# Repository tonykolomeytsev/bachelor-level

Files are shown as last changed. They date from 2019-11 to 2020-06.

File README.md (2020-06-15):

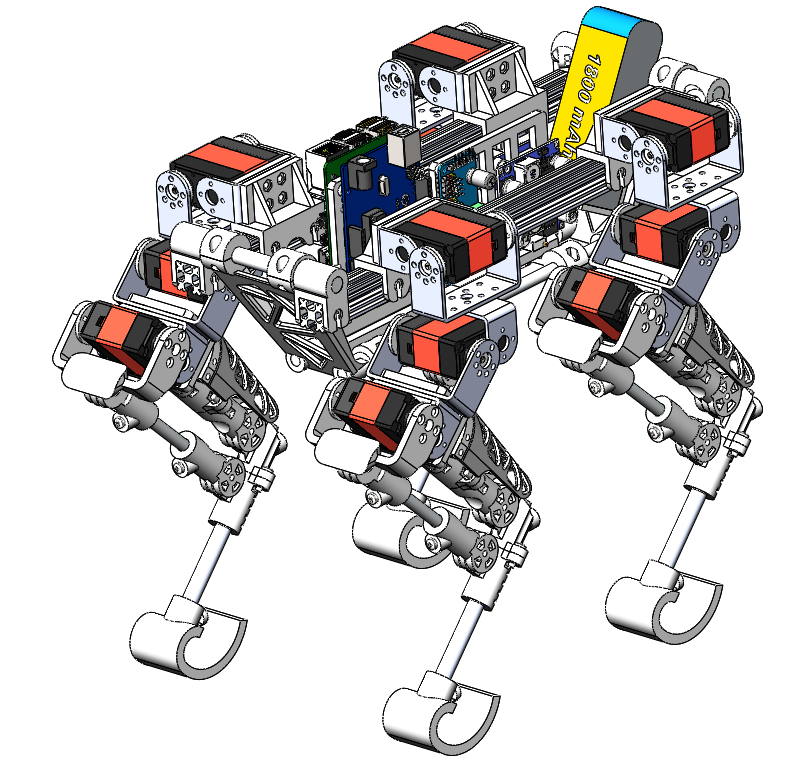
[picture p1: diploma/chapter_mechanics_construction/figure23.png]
Robot drawings


# Бакалаврская работа по разработке прототипа шагающего робота

### О чем вообще работа

В рамках работы рассматривается разработка шагающего четырехногого робота, с упором на проблему разработки конечностей и программирования. Спроектированы трёхмерные твердотельные чертежи системы, собрана физическая модель. Обоснован выбор конструктивных решений, выбор программной архитектуры, выбор алгоритмов. Применены лучшие практики работы с кодом, разработаны программные библиотеки для управления микроконтроллерами в составе робота.

### Материалы

Текст дипломной работы пишется в LATEX. Скомпилированный текст работы можно скачать [здесь](https://github.com/tonykolomeytsev/bachelor-level/raw/master/diploma/index.pdf).

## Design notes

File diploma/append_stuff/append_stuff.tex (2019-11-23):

\append{Комплектующие}
\label{appendix:stuff} % TODO починить нумерацию приложений в ref

\newcommand{\stuffitem}[3]{
    \textbf{#1}\newline
    \begin{tabular}[b]{cc}
         & \begin{tabular}[b]{rl} #3 \end{tabular}
    \end{tabular}
}

\stuffitem{Бесколлекторный двигатель BGM5208-200-12}
{append_stuff/bgm5208_200_12.jpg}
{
    Количество полюсов: & 12 \\
    Внутренний диаметр: & 12мм \\
    Вес: & 85г \\
    Размер: & 63х24мм \\
    Внутр. сопротивление: & 15 Ом
}

\vspace{0.5cm}
\stuffitem{Микрокомпьютер Raspberry Pi 3B}
{append_stuff/rpi.jpg}
{
    Процессор: & Broadcom BCM2837 \\
    Количество ядер: & 4 \\
    Частота процессора: & 1.2ГГц \\
    Разрядность: & 64 бита \\
    Оперативная память: & 1 ГБ \\
    Интерфейсы: & 4xUSB, Ethernet \\
    Напряжение питания: & 5В 
}

\vspace{0.5cm}
\stuffitem{Микроконтроллер STM32 Nucleo F429ZI}
{append_stuff/stm32.jpg}
{
    Ядро: & Cortex M4 \\
    Рабочая частота: & 84 МГц \\
    Разрядность: & 32 бита \\
    Цифровых пинов: & 81 шт. \\
    Кол-во шин: & 3xi2C, 4xSPI \\
    Напряжение питания: & 5В
}

\begin{center}
    \vspace{1cm}
    Продолжение приложения А на следующей странице... \newpage
    Продолжение приложения А...
\end{center}

\vspace{0.5cm}
\stuffitem{Блок питания KMPS05}
{append_stuff/kmps05.png}
{
    Ядро: & Cortex M4 \\
    Рабочая частота: & 84 МГц \\
    Разрядность: & 32 бита \\
    Цифровых пинов: & 81 шт. \\
    Кол-во шин: & 3xi2C, 4xSPI, 3xUART \\
    Напряжение питания: & 5В
}

\vspace{0.5cm}
\stuffitem{Драйвер бесколлекторных двигателей KMBD01}
{append_stuff/kmps05.png}
{
    Ядро: & Cortex M4 \\
    Рабочая частота: & 84 МГц \\
    Разрядность: & 32 бита \\
    Цифровых пинов: & 81 шт. \\
    Кол-во шин: & 3xi2C, 4xSPI, 3xUART \\
    Напряжение питания: & 5В
}

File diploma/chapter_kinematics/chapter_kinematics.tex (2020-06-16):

\chapter{\MakeUppercase{Кинематика конечностей робота}}
\section{Общее положение} \label{sec:kin_general}
Как было сказано ранее, оптимизация распределения массы робота потребовала введения в кинематическую структуру ноги замкнутого контура.
Проблема такой кинематики в механической сложности ее реализации с точки зрения конструктора. Из-за особенностей и требований, описанных в пункте \ref{sec:leg_design}, конструкция ноги получилась, как на рисунке ниже.
\begin{figure}[h]
    \centering
    
    \caption{Чертеж конструкции ноги}
    \label{}
\end{figure}

Для упрощения понимания ниже приведена трехмерная кинематическая схема конечности \ref{fig:kin_scheme}.
\begin{figure}[h] %h!
    \centering
    
    \caption{Трехмерная кинематическая схема ноги робота}
    \label{fig:kin_scheme}
\end{figure}

В составе конечности присутствует непрямой кинематический четырехзвенник (три из четырех сторон имеют разные длины). Это усложнило кинематическую задачу, сделало ее менее тривиальной. Как оказалось далее, наличие четырехзвенной передачи сделало невозможным нахождение аналитического решения обратной задачи кинематики. 

На кинематической схеме отмечены величины, численные значения которых приведены ниже:
\begin{align*} % миллиметры вместо метров и знаки препинания
    a_0&=0 \: мм, \\
    a_1&=46.22 \: мм, \\
    a_2&=20 \: мм, \\
    a_3&=44 \: мм, \\
    a_4&=20 \: мм, \\
    a_5&=27 \: мм, \\
    a_6&=87 \: мм, \\
    a_7&=107 \: мм, \\
    a_8&=12.62 \: мм, \\
    a_9&=24.5 \:  мм, \\
    a_{10}&=110  \: мм
\end{align*}

Заметим, что углы $ \varphi_3 $ и $ \varphi_4 $ различаются из-за того что $ a_5 \neq a_9 $. 

Допустимыми диапазонами рабочих углов являются:
\begin{align*}
    \varphi_1&=0 \dots \frac \pi 8, \\
    \varphi_2&=-\frac \pi 2 \dots 0 ,\\
    \varphi_3&=-\frac \pi 4 \dots \frac \pi 4.
\end{align*}

\noindent здесь границы диапазонов выбраны с запасом, чтобы предотвратить соударения составных частей ноги друг с другом. Диапазон для угла $ \varphi_4 $ не указан, поскольку он зависит от $ \varphi_3 $. 

\section{Общее решение четырёхзвенника} \label{sec:pre_direct_kin}

При построении аналитического решения четырехзвенной передачи было важно подобрать функции так, чтобы для рабочих диапазонов углов $ \varphi_1, \varphi_2, \varphi_3 $ не возникало переходов через ноль, или через бесконечно большие числа. Важно избежать использования кусочных функций и условных операторов для упрощения программирования.
Малые диапазоны углов в рассматриваемой конечности облегчают эту задачу.

На рисунке \ref{fig:scheme_four} приведена схема четырехзвенника. Найдем зависимость $ \varphi_4 $ от $ \varphi_3 $. Здесь $ l= a_4 + a_6=a_7 $ введен для упрощения расчётных формул, т.к. две стороны четырехзвенника имеют одну длину.
\begin{figure}[h]
    \centering
    
    \caption{Четырехзвенник}
    \label{fig:scheme_four}
\end{figure}

Сначала найдем диагональ $d$ по теореме косинусов, для того чтобы выразить противолежащие углы:
\begin{align}
    d = \sqrt{a_5^2 + l^2 - 2a_5 l \cos(\varphi_3)}. \label{eq:kin_1}
\end{align}

\noindent Выразим углы:
\begin{align}
    \gamma &= \text{arcsin}\left(\frac{a_5}{d}\cos \varphi_3\right) \label{eq:gamma}, \\
    \delta &= \text{arccos}\left(\frac{d^2+a_9^2-l^2}{2 a_9 l}\right). \label{eq:delta}
\end{align}

\noindent И искомый угол $ \varphi_4 $ будет находиться следующим образом:
\begin{align}
    \varphi_4 = \pi - \gamma - \delta. \label{eq:phi4_simple}
\end{align}

\noindent Подставим результаты \ref{eq:kin_1}, \ref{eq:gamma}, \ref{eq:delta} в уравнение \ref{eq:phi4_simple} и получим зависимость $ \varphi_4 $ от $ \varphi_3 $:
\begin{multline}
    \varphi_4 = \pi - \text{arcsin}\left(\frac{a_5}{\sqrt{a_5^2 + l^2 - 2a_5 l \cos(\varphi_3)}}\cos \varphi_3\right) - \\ - \text{arccos}\left(\frac{a_5^2 + l^2 - 2a_5 l \cos(\varphi_3)+a_9^2-l^2}{2 a_9 l}\right) .
\end{multline}

\section{Прямая кинематика}\label{sec:direct_kinematics}
Используя найденную в пункте \ref{sec:pre_direct_kin} связь, найдем решение задачи о положении точки $ A $. Трехмерная кинематическая схема приведена на рисунке \ref{fig:kin_scheme}. Зафиксируем сначала первую степень свободы ($ \varphi_1 = 0 $) и найдем координаты точки $ A $ в плоскости, параллельной плоскости $ XZ $:
\begin{multline}
    X_A=a_2+a_3\cos(\varphi_2)+a_6\sin(\varphi_2)-\\-a_8 \cos(\varphi _2+\varphi _4)+(a_9+a_{10}) \sin(\varphi _2+\varphi _4) ,
\end{multline}
\begin{multline} % написать вертикальную черту и phi1=0
    Z_A\Bigr|_{\varphi_1=0} =a_1-a_3 \sin(\varphi _2)+a_6 \cos(\varphi _2)+\\+a_8 \sin(\varphi _2+\varphi _4)+(a_9+a_{10}) \cos(\varphi _2+\varphi _4).
\end{multline}

\noindent Если мы предположим, что $ \varphi_1 = \frac \pi 2 $, тогда конечность будет <<поднята над землей>> в таком положении. Координата $ Z $ точки $ A $ станет равна нулю, координата $ Y $ увеличится. Так как от $ \varphi_1 $ зависят только координаты $Y$ и $Z$, получим следующие уравнения для координат точки $A$:
\begin{multline}
    X_A=a_2+a_3\cos(\varphi_2)+a_6\sin(\varphi_2)-\\-a_8 \cos(\varphi _2+\varphi _4)+(a_9+a_{10}) \sin(\varphi _2+\varphi _4) ,
\end{multline}
\begin{multline}
    Y_A=a_0+\sin(\varphi_1)[a_1-a_3 \sin(\varphi _2)+a_6 \cos(\varphi _2)+\\+a_8 \sin(\varphi _2+\varphi _4)+(a_9+a_{10}) \cos(\varphi _2+\varphi _4)] ,
\end{multline}
\begin{multline}
    Z_A=\cos(\varphi_1)[a_1-a_3 \sin(\varphi _2)+a_6 \cos(\varphi _2)+\\+a_8 \sin(\varphi _2+\varphi _4)+(a_9+a_{10}) \cos(\varphi _2+\varphi _4)].
\end{multline}

\noindent Таким образом, прямая задача кинематики решена.

Получив решение прямой задачи кинематики построим <<рабочую область>> ноги в системе координат связанной с корпусом. Если зафиксировать первую степень свободы, $ \varphi_1 = 0 $, то рабочая область ноги будет лежать в плоскости $ XZ $ (рисунок~\ref{fig:rab_obl}).
\begin{figure}[h]
    \centering
    
    \caption{Сечение рабочей области конечности робота}
    \label{fig:rab_obl}
\end{figure}

Следует отметить, что из-за того что $ a_9 < a_5 $, диапазон углов $ \varphi_4 $ получился шире, чем у $ \varphi_3 $. Это наглядно можно продемонстрировать на проекции ноги на плоскость $ XZ $. На рисунке~\ref{fig:leg_model} синей точкой отмечено реальное положение точки $ A $. Красной точкой отмечено положение точки $ A $ в том случае, если бы в четырехзвеннике $ a_5 $ был равен $ a_9 $. В крайних положениях третье звено конечности поворачивается на угол немного больший, чем угол поворота вала сервопривода. C использованием формулы прямой кинематики на рисунке~\ref{fig:leg_model} были изображены предельные положения последнего звена.
\begin{figure}[ht]
    \centering
    % левая картинка
    \begin{subfigure}[b]{0.45\textwidth}    
        \centering
        
        \caption{}
    \end{subfigure}
    % правая картинка  
    \begin{subfigure}[b]{0.45\textwidth}
        \centering
        
        \caption{}
    \end{subfigure}

    \captionsetup{justification=centering}
    \caption{Проекция ноги на плоскость $ XZ $: \\ (a) третье звено полностью <<разогнуто>>; \\ (б) третье звено полностью <<согнуто>>.}
    \label{fig:leg_model}
\end{figure}

Так, за счет использования четырехзвенной передачи, увеличена рабочая область конечности. На рисунке \ref{fig:fig7} серая область -- рабочая область при $ a_5 = a_9 $, зеленая область -- расширение рабочей области при $ a_5 > a_9 $.
\begin{figure}[h]
    \centering
    
    \caption{Сравнение рабочих областей}
    \label{fig:fig7}
\end{figure}

\section{Обратная кинематика} \label{sec:inverse_kin}
Как уже упоминалось ранее в пункте \ref{sec:kin_general}, аналитическое решение для задачи обратной представляет большую сложность. Это значит что нужно использовать численные методы решения.

Найдем решение обратной задачи кинематики с помощью метода Ньютона.

Кратко опишем суть метода Ньютона для решения системы нелинейных уравнений. 

Пусть дана система из $ n $ нелинейных уравнений с $ n $ неизвестными:
\[
\left\{ 
\begin{array}{c}
    f_1(x_1, \dots, x_n) = 0, \\
    f_2(x_1, \dots, x_n) = 0, \\
    \vdots \\
    f_i(x_1, \dots, x_n) = 0, \\
\end{array} 
\right.
\]

\noindent где $ f_i(x_1,\dots,x_n): \mathbb{R}^n \rightarrow \mathbb{R}, i=1,\dots, n $ -- нелинейные функции, определенные и непрерывно дифференцируемые в некоторой области $ G \subset \mathbb{R}^n $. Для записи в векторном виде введем величины:
\begin{align*}
    \overline{x} &= [x_1, x_2, \dots x_n]^T, \\
    F(x) &= [f_1(x), f_2(x),\dots,f_n(x)]^T = 0
\end{align*}

Нужно найти такой вектор $ \overline{x}^*=[x_1^*, x_2^*, \dots x_n^*]^T $, чтобы было верно равенство $ F(\overline{x}^*) = 0 $. 

Решение уточняется с помощью итерационной процедуры:
\begin{align*} % 
    x^{(k+1)}=x^{(k)}-J^{-1}(x^{(k)}) \cdot F(x^{(k)}),
\end{align*} % уточнить что такое k

\noindent где $ k=1,2\dots $ -- номер итерации, $ x^{(k)} $ -- $k$-е приближение к корню $ \overline{x}^* $, а $ J $ -- матрица Якоби:
\begin{align*}
    J = \begin{bmatrix}
        \frac{\partial f_1}{\partial x_1} & \dots & \frac{\partial f_1}{\partial x_n} \\
        \vdots & \ddots & \vdots \\
        \frac{\partial f_n}{\partial x_1} & \dots & \frac{\partial f_n}{\partial x_n}
    \end{bmatrix}.
\end{align*}

Применительно к задаче, рассматриваемой в данной работе, вектор $ \overline{x} $ является  вектором углов $ \overline{\varphi} = [ \varphi_1, \varphi_2, \varphi_3 ]^T $. Вектор $ F(x) $ -- это правая часть уравнений прямой кинематики.
\begin{equation*}
    F(\overline{\varphi}) = [ X_A(\overline{\varphi}) - X_A^*, Y_A(\overline{\varphi}) - Y_A^*, Z_A(\overline{\varphi}) - Z_A^* ]^T,
\end{equation*}
где $ X_A^*, Y_A^*, Z_A^* $ -- координаты целевого положения точки $A$.

В качестве критерия остановки итераций используется выполнение условия $ \norm{F(\varphi^{(k)}) - F^* } < \varepsilon $, где $\varepsilon $ -- заданная точность позиционирования.

Алгоритм поиска решения обратной задачи представлен ниже. В нём $ \varphi^{(0)} $ -- начальное приближение, $ \varepsilon $ -- точность вычислений, $ i $ -- число итераций (перед выполнением алгоритма устанавливается равным нулю).
\begin{itemize}
    \item[1.] Расчёт Якобиана $$ J = \begin{bmatrix}
        \frac{\partial X_A}{\partial \varphi_1} & 
        \frac{\partial X_A}{\partial \varphi_2} & 
        \frac{\partial X_A}{\partial \varphi_3} \\ \\
        \frac{\partial Y_A}{\partial \varphi_1} & 
        \frac{\partial Y_A}{\partial \varphi_2} & 
        \frac{\partial Y_A}{\partial \varphi_3} \\ \\
        \frac{\partial Z_A}{\partial \varphi_1} & 
        \frac{\partial Z_A}{\partial \varphi_2} & 
        \frac{\partial Z_A}{\partial \varphi_3}
    \end{bmatrix} $$ с использованием формул численного дифференцирования (аналитическая зависимость очень громоздкая).
    \item[2.] Вычисление погрешности: $$ r=F(\varphi^{(k)}). $$
    \item[3.] Вычисление вектора полного шага: $$ p = J^{-1} \cdot r $$ где $ J^{-1} $ -- обратная матрица Якобиана.
    \item[4.] Расчет следующего приближения: $$ \varphi^{(i+1)}=\varphi^{(i)} - p. $$ 
    \item[5.] Если заданная точность не достигнута и не превышен лимит на количество итераций, возвращаемся к пункту 1.
\end{itemize}

\noindent На практике оказалось, что скорость сходимости и сама сходимость сильно зависят от начального приближения. После реализации алгоритма были выявлены две проблемы в его работе:
\begin{itemize}
    \item[1.] Невозможно подобрать такие начальные приближения, при которых бы метод сходился во всем трехмерном пространстве рабочей области.
    \item[2.] В областях, в которых метод сходился в большом удалении от начального приближения, требовалось более 15 итераций для нахождения решения с заданной точностью.
\end{itemize}

\noindent Вторая проблема связана с производительностью вычислений, которые нужно производить на микрокомпьютере в режиме реального времени. Быстрое решение обратной задачи для любой точки трехмерной рабочей области -- это основное требование которое ставилось в начале разработки системы, поэтому итеративное приближение из предыдущих точек не  подходит в данной ситуации. В следующем пункте приведено решение возникших проблем.

\section{Оптимизация численного решения обратной задачи}

Путем проб и ошибок было решено сохранять в памяти (кэшировать) результаты вычислений прямой кинематики во время запуска программы. Проще говоря, подготовить набор заранее рассчитанных начальных приближений, которые будут использоваться от момента запуска робота до момента завершения работы. Во время решения обратной задачи нужно искать в кэш-таблице ближайшее готовое решение, принимать его за начальное условие текущей задачи и от него досчитывать более точное решение.

В качестве первой реализации две сотни предрассчитанных решений были помещены в кэш-таблицу. Каждая запись в таблице имеет две колонки. В первой колонке помещается вектор координат $ [X_A,Y_A,Z_A] $, во второй колонке вектор соответствующих им углов звеньев $ [\varphi_1, \varphi_2, \varphi_3] $. В момент поиска наилучшего начального приближения для некоторого положения конечности $ [X_A^*,Y_A^*,Z_A^*] $ находится такая запись кэш-таблицы, для которой евклидово расстояние между $ [X_A^*,Y_A^*,Z_A^*] $ и $ [X_A,Y_A,Z_A] $ будет минимально. 

\noindent Простейшая реализация кэширования решений обратной кинематики:

\begin{python}
def cache_inversed_kinematics():
    global cache
    cache = []
    phi1_start, phi1_end = PHI1_RANGE
    phi2_start, phi2_end = PHI2_RANGE
    phi3_start, phi3_end = PHI3_RANGE
    
    for phi1 in np.linspace(phi1_start, phi1_end, num=2):
        for phi2 in np.linspace(phi2_start, phi2_end, num=10):
            for phi3 in np.linspace(phi3_start, phi3_end, num=10):
                angles = [phi1, phi2, phi3]
                cache.append((direct(angles), np.array(angles)))
\end{python}

\noindent Пример реализации поиска решения в кэше:

\begin{python}
def find_nearest_solution(coordinates):
    global cache
    return min(cache, key=lambda di: np.linalg.norm(
        (coordinates - di[0]), 
        ord=2
    ))[1]
\end{python}

Так, получилось решить сразу две проблемы, описанные в пункте \ref{sec:inverse_kin}. Теперь на всей рабочей области обеспечена сходимость алгоритма. Поиск по кэш-таблице гораздо менее затратен, чем итерации метода Ньютона, а после того как найдено <<ближайшее>> решение, метод Ньютона быстро досчитывает ответ в среднем за 2-3 итерации.

\noindent Реализация функции поиска решения обратной задачи выглядит так:
\begin{python}
def inversed(coordinates):
    """ 
    Param coordinates is [X, Y, Z] numpy vector, in meters.
    This function uses Newton's numerical method.
    """
    phis = find_nearest_solution(coordinates)
    error = np.ones((3,), dtype=np.float64)
    i = 0
    while np.linalg.norm(error, 2) > 1e-5 and i < 100:
        J = jacobian(phis)
        X = direct(phis)
        error = X - coordinates
        p = np.matmul(np.linalg.pinv(J), error)
        phis = phis - p
        i += 1
    
    return phis
\end{python}

\textbf{Пути для дополнительной оптимизации:}
\begin{itemize}
    \item[1.] Проследить за равномерным распределением кэшированных решений в пространстве рабочей области. В случае равномерного распределения, размер кэша можно сильно уменьшить. Это ускорит поиск по таблице.
    \item[2.] Уменьшать количество кэшированных решений до тех пор пока метод Ньютона продолжает быстро сходиться. Это так же позволит сократить размер кэша и увеличить скорость поиска по нему.
    \item[3.] Найти максимальное значение точности $ \varepsilon $ с учетом ошибок сервоприводов и люфтов конструкции робота. 
\end{itemize}

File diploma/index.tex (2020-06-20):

\documentclass[a4paper,14pt,russian]{extreport}

\usepackage{extsizes}       % для установки размера шрифта
\usepackage{mathtext}       % русские буквы в формулах
\usepackage{cmap}           % поиск в pdf
\usepackage[T2A]{fontenc}   % кодировка
\usepackage[utf8]{inputenc} % кодировка исходного текста
\usepackage[russian]{babel} % локализация и переносы
\usepackage{pscyr}

% далее две строки отвечающие за т.н. "полуторный интервал"
% плюс исправляем кабанические отступы вокруг формул
\usepackage[nodisplayskipstretch]{setspace}
\onehalfspacing
% двойной оттступ - эквивалент интервала который в ворде называют "1.5 отступ"
% но я буду юзать ИСТИННЫЙ полуторный интервал, который на 10% меньше
%\doublespacing 
\parskip 1.5ex % paragraph spacing
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
\usepackage{listings}
\definecolor{mygray}{rgb}{0.5,0.5,0.5} % цвет комментариев
\definecolor{mygreen}{rgb}{0.1,0.6,0.1} % цвет номеров строк
\definecolor{mypurple}{rgb}{0.7,0.1,0.4} % цвет номеров строк
% настройка общего внешнего вида для всех языков
\lstset{breaklines=true,
        basicstyle=\footnotesize\ttfamily,
        commentstyle=\color{mygreen},
        keywordstyle=\bfseries\color{blue},
        stringstyle=\bfseries\color{mypurple},
        numbers=none} %left}
        %numberstyle=\color{mygray},
        %numbersep=20pt}
% Окружения для разных языков программирования
\lstnewenvironment{python}[1][]{\lstset{language=Python,#1}}{}
\lstnewenvironment{cpp}[1][]{\lstset{language=C,#1}}{}
\lstnewenvironment{code}[1][]{\lstset{#1}}{} % для любого кода

% ====================================================================
%                 Организация рабочего пространства
% ====================================================================
\usepackage{import}
\newcommand{\includechapter}[1]{\subimport{chapter_#1/}{chapter_#1}\newpage}
\newcommand{\includeappend}[1]{\subimport{append_#1/}{append_#1}\newpage}
\usepackage{tabularx}

% ====================================================================
%                         Список литературы
% ====================================================================
\newcommand{\includebiblio}[1]{
    \begingroup
    \renewcommand{\chapter}[2]{
        \clearpage
        \stepcounter{chapter}
        \centering\paragraph{\MakeUppercase{Библиографический список}}
        \addcontentsline{toc}{likechapter}{\MakeUppercase{Библиографический список}}
    }
    \let\bibfont\protect\normalsize
    \bibliographystyle{ugost2008} % Стиль библиографических ссылок БибТеХа
    \bibliography{#1}
    \endgroup
}

% ====================================================================
%                           Приложения
% ====================================================================
\usepackage[title,titletoc]{appendix}
\titleformat{\paragraph}[display]
    {\filcenter}
    {\MakeUppercase{\chaptertitlename} \thechapter}
    {8pt}
    {\bfseries}{}
\titlespacing*{\paragraph}{0pt}{-30pt}{8pt}
\newcommand{\append}[1]{
    \clearpage
    \stepcounter{chapter}
    \begin{center}
        \paragraph{\MakeUppercase{\chaptertitlename~\Asbuk{chapter}}}
        \vspace{-0.5cm}
        \paragraph{\MakeUppercase{ #1}}
    \end{center}
    \addcontentsline{toc}{likechapter}{\MakeUppercase{\chaptertitlename~\Asbuk{chapter}: #1}}
}

% ====================================================================
%             Счетчики страниц, таблиц, изображений
% ====================================================================
\usepackage{lastpage} % использовать можно \pageref*{LastPage}
% далее костыль со stackoverflow
\usepackage{totcount}
\newcounter{totfigures}
\newcounter{tottables}
\makeatletter
    \AtEndDocument{
      \addtocounter{totfigures}{\value{figure}}
      \addtocounter{tottables}{\value{table}}
      \immediate\write\@mainaux{
        \string\gdef\string\totfig{\number\value{totfigures}}
        \string\gdef\string\tottab{\number\value{tottables}}   
      }
    }
\makeatother
% перед каждым вызовом chapter обновляем счетчики
\usepackage{etoolbox}
\pretocmd{\chapter}{\addtocounter{totfigures}{\value{figure}}}{}{}
\pretocmd{\chapter}{\addtocounter{tottables}{\value{table}}}{}{}

% ====================================================================
%                           МЕТА-ДАННЫЕ
% ====================================================================
\usepackage{authblk}
\author{Коломейцев А.А.}
\title{Разработка прототипа четырехногого шагающего робота}
\affil{НИУ "МЭИ"}

\newcommand{\fixme}{\color{red} \textbf{FIXME} \color{black}}
\usepackage{pdfpages}

% ====================================================================
%                           НАЧАЛО КОНТЕНТА
% ====================================================================
\begin{document}

\setcounter{page}{4}

\includechapter{annotation} % аннотация

% Оглавление. 
% Для правильного отображения оглавления документ должен быть
% скомпилирован дважды (иногда трижды).
\tableofcontents\newpage

\includechapter{intro} % введение

\includechapter{legged_robots}

\includechapter{mechanics_construction}

\includechapter{kinematics}

% \includechapter{body_orientation} % на удаление

\includechapter{walking_model} % вернуть после ревью

\includechapter{arch}

\includechapter{conclusion}

%\includechapter{system_analisys} % глава "Анализ системы"

\includebiblio{sources} % в файле source.bib лежит БД со списком источников

%Дипломная работа \pageref{LastPage}~с \totfig~рис. \tottab~таблиц.

\appendix

\newpage
\addcontentsline{toc}{likechapter}{ПРИЛОЖЕНИЕ А: ПОСТРОЕНИЕ РАБОЧЕЙ ОБЛАСТИ}
\includepdf[pages={1,2}]{append1.pdf}

% \includeappend{stuff}

% \append{Код класса}
% \lstinputlisting[language=Python,firstline=14,lastline=34,firstnumber=14]{asynclapi.py}

\end{document}

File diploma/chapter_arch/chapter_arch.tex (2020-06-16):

\chapter{\MakeUppercase{Программная архитектура}} \label{chap:arch}
\section{Структура управления}

Высокоуровневая логика запрограммирована на микрокомпьютере \textit{Rasp}-\textit{berry Pi}. Тот в свою очередь отправляет последовательность команд на платформу \textit{Arduino}, которая управляет сервоприводами через специальный драйвер и отправляет информацию о своем состоянии в виде обратной связи на микрокомпьютер. Упрощенная схема реализованной системы приведена на рисунке \ref{fig:upravlenie}.

\begin{figure}[h!]
    \centering
    
    \caption{Упрощенная схема системы управления робота}
    \label{fig:upravlenie}
\end{figure}

\section{Протокол передачи данных} \label{sec:protocol}
Отправка команд от \textit{Raspberry Pi} к \textit{Arduino} и последующий прием обратной связи производится через интерфейс \textit{Serial}. Это самый надежный вариант при условии, что для установки соединения используется обыкновенный \textit{USB} кабель, который уже защищен от помех и штекер которого надежно закреплен в разъеме.

Для достижения наилучшей скорости реакции микроконтроллера на команды был разработан специальный протокол передачи данных и были написаны легковесные программные библиотеки. Для платформы \textit{Arduino} код написан на языке \textit{C++}, для микрокомпьютера \textit{Raspberry Pi} была разработана библиотека на языке \textit{Python}.

\noindent Библиотека для передачи данных написана для трёх платформ. Она сильно упрощает наладку управления \textit{Arduino} с помощью \textit{Raspberry Pi}. Основная идея программного кода в том, чтобы микрокомпьютер отправлял на микроконтроллер очень простые команды, состоящие из массива байт, в который зашифрованы лишь целочисленный номер и вещественные аргументы. Обратная связь от микроконтроллера реализована в формате \textit{JSON}.

\begin{figure}[h]
    \centering
    
    \caption{Управление микроконтроллерами с помощью \textit{Raspberry Pi}}
    \label{}
\end{figure}

\textbf{Для справки}: \textit{JSON} это сокращение от \textit{JavaScript Object Notation} -- формата передачи данных. Как можно понять из названия, \textit{JSON} произошел из \textit{JavaScript}, но он доступен для использования на многих других языках, включая \textit{Python, Ruby, PHP} и \textit{Java}, в англоязычным странах его в основном произносят как \textit{Jason}, то есть как имя Джэйсон. Легкочитаемый и компактный, \textit{JSON} представляет собой хорошую альтернативу \textit{XML} и требует куда меньше форматирования контента \cite{Jayson2018}.

\noindent Объект \textit{JSON} это набор данных в формате <<ключ-значение>>, который находится в фигурных скобках.
Вот так выглядит \textit{JSON} объект:
\begin{code}
{
  "first_name" : "Anton",
  "last_name" : "Kolomeytsev",
  "location" : "Moscow",
  "online" : true,
  "languages" : ["Russian", "English"] 
}
\end{code}

Массив байт, отправляемый на микроконтроллер, всегда имеет одну и ту же структуру, которую легко расшифровать. Каждая команда имеет свой идентификатор (число от 0 до 255), а также может не иметь вовсе, либо иметь ограниченное числом $ 256^4 $ количество аргументов. 

При отправке инструкции на микроконтроллер первым байтом всегда идет номер (идентификатор) команды. Вторым байтом идет число -- количество аргументов. Если у команды нет аргументов, байт нулевой. Пример команды без аргументов с идентификатором $ 207 $:
\begin{equation*}
    \overbrace{11001111}^{идентификатор\: команды} \underbrace{00000000}_{количество\: аргументов}
\end{equation*}

К каждому идентификатору можно привязать выполнение роботом какого-либо действия. Например, включение или выключение компрессора, и т.д. Но бывает, что нужно уточнить параметры выполнения команды какими-то числовыми аргументами. В таком случае второй байт будет ненулевым и он будет указывать на количество идущих после второго байта блоков длиной в 4 байта. В каждом таком четырёхбайтном блоке хранится вещественное число. Пример команды с идентификатором $ 209 $ с одним вещественным аргументом:
\begin{equation*}
    \overbrace{11010001}^{идентификатор\: команды} \underbrace{00000001}_{количество\: аргументов} \overbrace{10110001 \;\; 11100010 \;\; 00110100 \;\; 00100100}^{вещественный \: аргумент}
\end{equation*}

Описанным образом можно реализовать команду, которой передаются, например, требуемые скорости вращения колес, или параметры чувствительности датчиков, и т.д.

Преимущества выбранного подхода:
\begin{itemize}
    \item Микроконтроллер способен очень быстро расшифровать массив байт. Поэтому задержка между отправкой команды и её исполнением для человека не заметна.
    \item Невозможно перенести высокоуровневый функционал и принятие решений на микроконтроллер. Это заставляет продумывать структуру системы.
    \item При таком формате общения между устройствами разработка  укладывается в основы теории автоматического управления.
    \item Возможность подключить до четырёх микроконтроллеров к одному \textit{Raspberry Pi}.
\end{itemize}

\textbf{Протокол}

Правила, по которым устанавливается соединение, следующие:
\begin{itemize}
    \item[1.] \textit{Raspberry Pi} устанавливает соединение с \textit{Arduino} по \textit{USB}, открывая \textit{Serial} порт между устройствами.
    \item[2.] \textit{Arduino} отправляет свой уникальный идентификатор.
    \item[3.] После получения идентификатора \textit{Raspberry} может использовать его для обмена данными. 
\end{itemize}

При написании кода на \textit{Raspberry}, есть всего три простых функции:

\noindent Функция \textit{push}: отправляет команду под номером \textit{CODE} с аргументами \textit{ARG}
\begin{code}
clapi.device_id.push(CODE[, ARG1, ARG2, ..., ARGN])
\end{code}

\noindent Функция \textit{pull}: блокирует выполнение программы, дожидается входящего сообщения от устройства. Возвращает \textit{JSON}, который нам прислало устройство.
\begin{code}
clapi.device_id.pull()
\end{code}

\noindent Функция \textit{request}: отправляет команду как \textit{push}, после чего дожидается ответа как \textit{pull}.
\begin{code}
clapi.device_id.request(CODE[, ARG1, ARG2, ..., ARGN])
\end{code}

Первая версия кода библиотеки для управления была написана автором в 2019 году, использовалась <<в боевых условиях>> и достойно показала себя на робототехнических соревнованиях \textit{Eurobot} \cite{Kekmech2020}. С тех пор код был доработан, дополнительно протестирован и оптимизирован под новые нужды.

\section{Кинематические расчеты}

Перенос расчётов из систем математических расчетов вроде \textit{Matlab, SciLab} или \textit{Mathematica} на один из языков программирования это не всегда тривиальная задача. Самая сложная часть переноса -- матричные вычисления, элементы математического анализа (пределы, производные, интегрирование), решение систем СЛАУ, решение систем нелинейных уравнений. При переносе кинематических расчётов в рамках данного проекта понадобилось реализовать численно следующие функции:
\begin{itemize}
    \item вычисление задачи о положениях;
    \item решение тригонометрической задачи о четырехзвеннике;
    \item вычисление Якобиана;
    \item решение обратной задачи кинематики.
\end{itemize}

Использование библиотеки численной математики \textit{Numpy} на языке программирования \textit{Python} сильно упростило задачу. Стоит отметить, что \textit{Numpy} сегодня активно используется для математических вычислений исследователями всех стран \cite{Numpy2020}.

\subsection{Вычисление задачи о положениях}

Самая простая в реализации задача -- найти три координаты и вернуть вектор:
\begin{python}
def direct(angles):
    phi1, phi2, phi3 = angles[0], angles[1], angles[2]
    phi4 = four_link_angle(phi3) - (pi/2)
    X = A2 + A3 * cos(phi2) + A6 * sin(phi2) + A8 * sin(phi2 + phi4) + (A9 + A10) * cos(phi2 + phi4)
    V = A1 - A3 * sin(phi2) + A6 * cos(phi2) + A8 * cos(phi2 + phi4) - (A9 + A10) * sin(phi2 + phi4)
    Y = V * sin(phi1)
    Z = V * cos(phi1)
    return np.array([X, Y, Z])
\end{python}

\noindent Декомпозируем входные углы, подставляем их в формулы, получая $ X, Y, Z $, и возвращаем вектор $ F^* =[ X, Y, Z ] $.

\subsection{Решение задачи о четырехзвеннике}
Тоже не сложная задача, если есть готовое решение в математическом пакете \textit{Mathematica}.
\begin{python}
def four_link_angle(phi3):
    d = sqrt(A5**2 + A7**2 - 2 * A5 * A7 * cos(phi3 + pi/2))
    gamma = asin((A5 / d) * cos(phi3))
    delta = acos((d**2 + A9**2 - A7**2) / (2 * d * A9))
    return (pi - gamma - delta)
\end{python}

\noindent Вычисления здесь достаточно громоздкие, хотя угол $ \varphi_3 $ не сильно отличается от $ \varphi_4 $.

\subsection{Вычисление Якобиана}
Для численного решения обратной задачи кинематики нужно в каждой итерации вычислять Якобиан. Аналитический вид производной кинематического графа представленной в работе конечности неоправданно больших размеров, что делает невозможным его перенос из математического пакета в код на \textit{Python}. Однако используя функцию вычисляющую прямую задачу кинематики, и устанавливая шаг для приращения каждого угла мы можем дифференцировать численно следующим образом \cite{Morken2010}:
\begin{align*}
    \frac{\partial f}{\partial x}(a, b) &\approx \frac{f(a+h_1, b) - f(a, b)}{h_1}, \\ 
    \frac{\partial f}{\partial y}(a, b) &\approx \frac{f(a, b+h_2) - f(a, b)}{h_2}
\end{align*}

\noindent Можно оценить погрешность вычисления:
\begin{align*}
    \frac{\partial f}{\partial x}(a, b) - \frac{f(a+h_1, b) - f(a, b)}{h_1} &= \frac{h_1}{2} \frac{\partial^2 f}{\partial x^2}(c_1, b), \\ 
    \frac{\partial f}{\partial y}(a, b) - \frac{f(a, b+h_2) - f(a, b)}{h_2} &= \frac{h_2}{2} \frac{\partial^2 f}{\partial y^2}(a, c_2)
\end{align*}
\noindent Где $ c_1 \subset (a, a+h_1) $, а $ с_2 \subset (b, b+c_2) $. Такой результат нас вполне устраивает, поэтому реализация в коде следующая:
\begin{python}
def jacobian(angles):
    h = pi * 1e-4 # diff step
    F = direct(angles)
    eye = np.eye(3) * h # matrix with all h in diagonal elements
    dFdPhi1 = (direct(angles + eye[0]) - F) / h
    dFdPhi2 = (direct(angles + eye[1]) - F) / h
    dFdPhi3 = (direct(angles + eye[2]) - F) / h
    return np.array([dFdPhi1, dFdPhi2, dFdPhi3]).reshape((3, 3)).T
\end{python}

\noindent Для оптимизации вычисления идут сразу по строкам матрицы.
Решение обратной задачи кинематики уже было рассмотрено в пункте \ref{sec:inverse_kin}.

\section{Тестирование кода}

При разработке программной части любого устройства существует непропадающая проблема. Разработчики не могут писать код без ошибок. Более того, в сложных программных системах при внесении каких-либо изменений слишком сложно понять, как это отразится на других частях.

Для того, что бы минимизировать поиски ошибок в коде и ускорить их обнаружение, пишутся так называемые \textit{Unit}-тесты. Такие тесты сами по себе являются программами, но сильно более простыми, чем сама система. Эти тесты автоматически запускаются при внесении в код системы изменений и выводят предупреждения в случае неправильного поведения или логики работы системы.
Автоматические тесты -- это хороший тон в программировании.

В нашем случае, например, тесты запускают функции решающие задачи кинематики с разными входными данными и сверяют ответы с теми числами, которые заранее рассчитаны в \textit{Mathematica}. Если ответы не сходятся (с нужной точностью), нам покажут предупреждение. Таким образом ошибки, которые могли быть внесены в алгоритмы, связанные с кинематическими расчетами, будут выявлены до того, как код будет запущен на физической модели робота. Что повышает безопасность работы с такой системой.

Для тестирования кода на \textit{Raspberry Pi} используется библиотека \textit{PyTest}.

% \section{Абстракция над вычислениями}

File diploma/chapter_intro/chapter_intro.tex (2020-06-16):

\likechapter{Введение}

Шагающие роботы - это класс роботов, имитирующих движения людей и животных. Миллионы лет эволюции показывают, что передвижение при помощи ног это наиболее эффективный способ быстро приспосабливаться к плохим, неровным поверхностям. Сегодня от робототехнической шагающей системы требуется приспосабливаться к тем условиям, в которых она раньше не была. Рассмотрим существующих роботов, которые сегодня есть на рынке, и то, каким образом их разработчики решают эту задачу.

\textbf{Рынок шагающих роботов}

Классифицировать шагающие машины можно не только по количеству ног. Некоторые роботы комплектуются также и колесами, для увеличения скорости передвижения по ровным поверхностям. Для простоты, разделим рассматриваемых роботов на двуногих и четырехногих. 

На текущий момент можно найти огромное количество шагающих роботов. Гексаподы, робо-пауки и т.д. Но среди сотен моделей можно выделить таких, ходьба которых максимально приближена к животной.

Среди современных четырехногих роботов можно выделить:
\begin{itemize}
    \item роботы Spot и Spot-Mini от компании Boston Dynamics \cite{BostonDynamics2020} (рисунок~\ref{fig:intro1});
    \item робот Mini-Cheetah от студентов MIT \cite{Mit2020};
    \item Робот ANYmal от студентов Цюрихского университета \cite{ZurichETH2020} (рисунок~\ref{fig:intro2});
    \item робот HyQReal от IIT \cite{Iit2020} (Итальянского технологического института);
    \item роботы LaikaGo и AlienGo от компании Unitree Robotics \cite{Unitree2020}.
\end{itemize}

\begin{figure}[h!]
    \centering
    
    \caption{Робот \textit{Spot-mini} компании \textit{Boston Dynamics}}
    \label{fig:intro1}
\end{figure}

\begin{figure}[h!]
    \centering
    
    \caption{Робот \textit{ANYmal} университета \textit{ ETH Zurich}}
    \label{fig:intro2}
\end{figure}

Среди двуногих можно выделить такие проекты, как:

\begin{itemize}
    \item робот Digit от компаний Agility Robotics и Ford \cite{Agility2020_2} (рисунок~\ref{fig:intro3});
    \item робот Cassie от компании Agility Robotics \cite{Agility2020_2};
    \item робот Atlas от компании Boston Dynamics \cite{BostonDynamics2020}.
\end{itemize}

\begin{figure}[h]
    \centering
    
    \caption{Робот \textit{Digit} компании \textit{ Agility Robotics}}
    \label{fig:intro3}
\end{figure}

\begin{figure}[h]
    \centering
    
    \caption{Обучение ходьбе в симуляции робота \textit{LaikaGo} компании \textit{ Unitree Robotics} }
    \label{fig:intro4}
\end{figure}

Всех выше перечисленных роботов объединяет одна схожая особенность -- они обучены ходьбе при помощи новых, набирающих популярность, методов глубокого обучения. Алгоритм их ходьбы не описан статическими константами в коде, он создан при помощи обучения моделей искусственных нейронных сетей. Благодаря этому все они показывают высокую степень мобильности и адаптивности к окружающей среде. Далее, для некоторых из роботов, приведены используемые разработчиками методы обучения. Движения таких роботов при перемещении визуально похожи на движения животных со схожим механическим строением тела. 
Стоит отметить, что модели, обученные таким образом показывают более высокую эффективность при перемещении \cite{Hwangbo2019} и меньшее потребление энергии, чем модели ходьбы, описанные человеком вручную.

\begin{figure}[h!]
    \centering
    
    \caption{Множество моделей робота \textit{ANYmal} обучаются одновременно }
    \label{fig:intro5}
\end{figure}

Для обучения четырехногого робота LaikaGo используется помещенная в симуляцию физическая модель робота \cite{LaikaGo2019} (рисунок \ref{fig:intro4}). Робот ANYmal точно так же был <<натренирован>> при помощи многократных запусков его физической модели в симуляции. Чтобы ускорить процесс, разработчики поместили в симуляцию сразу множество физических моделей робота, которые тренировались одновременно \cite{RoboSysLab2019}. Такой способ позволил быстро, дешево и безопасно обучать робота ходьбе (демонстрация метода на рисунке~\ref{fig:intro5}). 

Такую же схему обучения используют для двуногого робота Cassie \cite{AgilityRobo2018}. Кроме того, разработчики из Agility Robotics используют машинное обучение еще и для планирования траектории, а также для правильного позиционирования стоп робота на неровной местности \cite{Agility2020}.

Для большинства приведенных выше четырехногих роботов можно также выявить одну общую особенность -- у них схожие кинематические схемы, у конечностей по три степени свободы. Отсутствие избыточных степеней свободы упрощает проектирование конечностей и разработку математических моделей их движения. Этот факт повлиял на конструкцию ног робота, которая была разработана в рамках данного проекта.

\section*{Актуальность работы}

Задача разработки шагающих роботов становится все более актуальной с каждым годом. Всё в большей степени людей стараются заменять шагающими роботами для работ, в которых требуется мобильность и подвижность человеческих ног, и при этом невозможно присутствие самого человека. Например, приведенные выше роботы создаются для инспекции строек и помещений, исследования местности вдали от дорог и цивилизации, помощи в устранении последствий катастроф, пребывания в опасной для человека среде (под воздействием вредных газов, излучения). Также недавно появился опыт применения таких роботов для уменьшения количества контактов между людьми во время эпидемии респираторного заболевания \cite{Bbc2020}. Открытость методик, исходных кодов и готовых моделей в открытом доступе приведет к массовой разработке шагающих роботов не только крупными предприятиями, но и частными разработчиками. 

%\fixme ОБЗОР РЫНКА И АНАЛИЗ ЛИТЕРАТУРЫ

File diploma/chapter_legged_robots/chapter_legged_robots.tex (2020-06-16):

\chapter{\MakeUppercase{Постановка задачи и план решения}}

\section{Задачи работы}

В рамках работы рассматривается разработка шагающего четырехногого робота, с упором на проблему проектирования конечностей и разработки программного обеспечения (ПО) для управления движением.

Для выполнения работы требуется:
\begin{itemize}
    \item Разработать общую кинематическую схему робота.
    \item Рассчитать худший (по нагрузке) статический случай для конечностей четырехногого робота.
    \item Подобрать электроприводы удовлетворяющие по крутящему моменту.
    \item Подобрать остальные комплектующие (управляющая электроника, детали корпуса, источник питания, проводка), входящие в состав робота и обеспечивающие его автономную работу.
    \item Спроектировать и собрать прототип робота.
    \item Разработать ПО для управления робота.
\end{itemize}

\section{Краткое описание кинематической схемы}

После изучения существующих на рынке роботов, было решено реализовать в прототипе наиболее распространенную конструкцию. Можно заметить что у всех приведенных моделей роботов почти одинаковая кинематика, характеризующаяся четырьмя конечностями, у каждой из которых по три степени свободы. Поэтому с опорой на опыт разработчиков роботов, о которых написано во введении, в качестве кинематической схемы прототипа была выбрана схема, продемонстрированная на рисунке \ref{fig:kin_scheme1}. 

Кинематика конечности подробнее рассматривается далее. Также далее конечности допустимо называть ногами, а точку $ A $ -- стопой робота. Изображенный на рисунке \ref{fig:kin_scheme1} параллелепипед -- это корпус, тело робота.

\begin{figure}[ht]
    \centering
    
    \caption{Кинематика четырехногого робота. Нумерация ног произвольная}
    \label{fig:kin_scheme1}
\end{figure}

% \fixme ИЛЛЮСТРАЦИЯ

\subsection{Определение максимальной нагрузки на приводы конечностей}

Расчет максимальной нагрузки производится при известных размерах комплектующих робота. Это объясняется тем, что чертежи изделия (рисунок \ref{fig:final_render}) были подготовлены до выбора приводов.

\begin{figure}[h]
    \centering
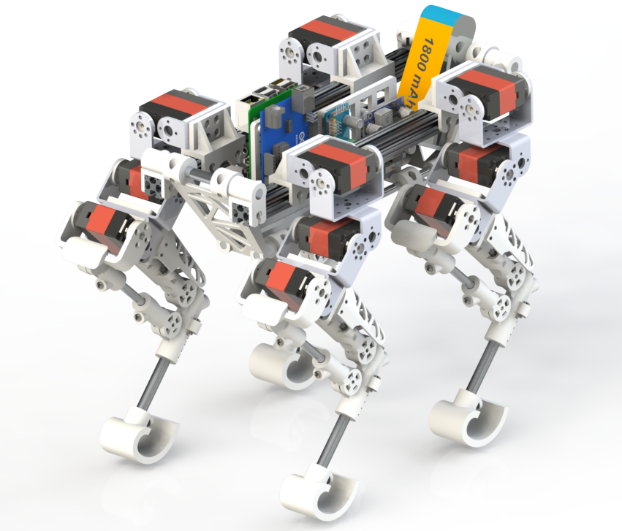
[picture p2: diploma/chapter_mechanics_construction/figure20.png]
    
    \caption{Сборочный чертеж робота.}
    \label{fig:final_render}
\end{figure}

У большей части доступных на рынке сервоприводов одинаковые габариты, форма корпуса и даже расположение крепежных отверстий. Разница лишь в крутящих моментах, характеризующихся передаточным числом редуктора. Отсюда следует, что чертежи таких приводов ничем не отличаются друг от друга и это позволяет размещать их в сборочном чертеже робота до того как станет известна нагрузка на приводы. После того как становится известен точный набор комплектующих и их вес, а также длины конечностей, мы можем выбрать сервопривод, удовлетворяющий требуемому крутящему моменту.

Найдем максимальную статическую нагрузку на приводы конечностей, рассмотрев наихудшую статическую конфигурацию робота. «Худшей» конфигурацией называется такая, при которой одному или нескольким приводам нужно приложить максимальный момент для поворота звена конечности в нужную сторону.

Конструкция ноги робота не позволяет разогнуть ее полностью. Поэтому можно привести длины звеньев конечности спроецированные на горизонтальную ось для того чтобы провести приблизительные расчеты:
\begin{align*}
    l_1 &\approx 131\: мм, \\
    l_2 &\approx 134.5\: мм
\end{align*}

Худшим случаем является случай, при котором робот лежит на «животе» с выпрямленными конечностями. Чтобы подогнуть под себя конечность, нужно будет преодолеть момент $M_{худш}$ с учетом массы тела робота $m_T$. При этом максимальный крутящий момент потребуется приводу, находящемуся в первом узле, или можно сказать, управляющему первой степенью свободы.

\begin{figure}[ht]
    \centering
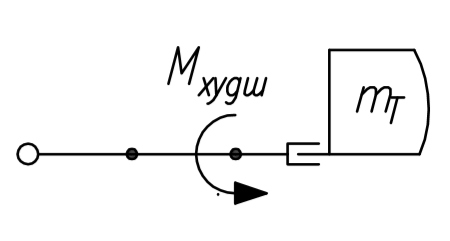
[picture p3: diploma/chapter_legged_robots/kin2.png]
    
    \caption{Иллюстрация худшего статического случая}
\end{figure}
% на рисунке показать реакцию опоры и mg

При расчёте в первом приближении можно пренебречь трением и весами звеньев. Также можно учесть, что нагрузка, создаваемая массой тела робота будет распределена равномерно по всем четырем ногам. Это значит что на одну ногу будет приходится четверть массы тела робота.

Самой тяжелой частью конструкции оказались каркас корпуса, в составе которого много алюминиевых профилей, и аккумулятор. Самые легкие составляющие конструкции -- это электронные компоненты. Суммарно все комплектующие корпуса весят $3.2$ кг. 

При таком расчете можно считать, что каждой ноге надо будет «поднять» около $ 0.8 $ кг веса. Тогда в худшем случае, приложенный момент вычисляется просто:
\begin{equation} \label{eq:statics1}
    M_{худш}= \frac 1 4 (l_{1}+l_{2}) m_T g, 
\end{equation}
\noindent здесь $l_1$ и $l_2$ - длины звеньев ноги.

При расчете по формуле \ref{eq:statics1} требуемый крутящий момент равен примерно $ 2.1  \: Н \cdot м$. После проведенного поиска среди доступных на рынке сервоприводов, был выбран сервопривод с крутящим моментом $ 2.5 \: Н \cdot м $. С таким сервоприводом максимально допустимый вес робота будет примерно равен $ 3.8 \: кг $.

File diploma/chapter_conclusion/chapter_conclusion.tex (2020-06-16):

\likechapter{\MakeUppercase{Заключение}}

В рамках работы разработана кинематическая схема четырехногого шагающего робота и рассчитан худший по нагрузке на конечности статический случай. С опорой на расчеты подобраны электроприводы удовлетворяющие крутящему моменту. Подобраны микрокомпьютер и микроконтроллер для управления роботом и вспомогательные электронные компоненты, обеспечивающие работоспособность робота. 

Спроектирован и собран прототип робота. Исследовано движение конечностей по простой траектории. Разработано управляющее программное обеспечение: на языке программирования Python написан модуль кинематических расчетов и библиотека для управления микроконтроллером; на языке С++ написана библиотека для обратной связи с микрокомпьютером. Был разработан протокол передачи данных между логическими устройствами в составе робота. Настроено окружение для тестирования и сборки кода. Выполнены все поставленные задачи.

В работе описан процесс создания прототипа шагающего робота, потенциал которого по улучшению и модернизации достаточно велик.

Доступные способы улучшения механических характеристик робота:
\begin{itemize}
    \item[1.] В проекте были использованы достаточно дешевые модели сервоприводов, которые сильно усложняют разработку управляющего программного обеспечения и снижают точность позиционирования конечностей. Замена таких приводов на более совершенные позволит производить управление не только по положению, но и по скоростям. Это позволит улучшить общие механические характеристики конечностей.
    \item[2.] Замена приводов на более совершенные позволит еще сильнее уменьшить габариты робота. 
\end{itemize}

Способы улучшения программного обеспечения:
\begin{itemize}
    \item[1.] Использовать алгоритмы машинного обучения вместо ручного задания траекторий движения конечностей.
    \item[2.] Применение искусственных нейронных сетей для обучения ходьбе в симуляции, как это делают ведущие разработчики шагающих роботов, приведенные в начале работы. 
\end{itemize}

Для улучшения электронной схемы следует начать применять печатные платы собственной разработки, включающие в свой состав микроконтроллеры, драйверы и преобразователи напряжений. Это позволит избежать проблем с коммутацией разнородных устройств друг с другом и их питанием.

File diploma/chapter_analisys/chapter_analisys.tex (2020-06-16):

\chapter{\MakeUppercase{Анализ проделанной работы}}

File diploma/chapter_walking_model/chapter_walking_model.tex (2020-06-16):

\chapter{\MakeUppercase{Моделирование ходьбы}}
\section{Траектории движения ног}

Самым простым способом реализации ходьбы является такой, при котором робот по очереди переставляет ноги в нужном порядке, всегда имея три точки опоры. Было решено для начала взять именно эту реализацию, и немного ее модернизировать. Стопы робота будут двигаться по запрограммированной заранее траектории, перемещаясь по точкам, лежащим на этой траектории.

Движение ноги во время ходьбы было описано при помощи двух замкнутых траекторий движения точки $ A $ в двух проекциях: на плоскость $ XZ $ и $ XY $. На полученных траекториях берется множество точек, в которые управляющей программой по очереди переносится точка $A$. В качестве первого приближения для траектории в проекции на плоскость $ XZ $ был выбран эллипс (рисунок \ref{fig:traj1}), для траектории в проекции на плоскость $ XY $ выбрана линия (эллипс с нулевой малой полуосью).

\begin{figure}[h]
    \centering
    
    \caption{Траектория описываемая точкой $A$ в рабочей области}
    \label{fig:traj1}
\end{figure}

Точки на этой траектории достаточно легко вычислять для каждого момента времени, если замкнутая кривая описана функцией. Следует отметить, что на практике абсолютный энкодер установленный в подобранных приводах имеет <<область нечувствительности>> (рисунок \ref{fig:nonff}). Это приводит к тому, что при слишком малом расстоянии между точками, выбранными на траектории, текущая и новая конфигурации ног слабо отличаются. Это в свою очередь приводит к тому, что двигатели просто <<игнорируют>> управляющий сигнал, сообщающий о необходимости поворота на новый, слабо отличающийся угол. Упрощенная схема работы сервопривода показана на рисунке \ref{fig:upr_servo}.

\begin{figure}[h]
    \centering
    
    \caption{Область нечувствительности отмечена красным цветом}
    \label{fig:nonff}
\end{figure}

\begin{figure}[h]
    \centering
    
    \caption{Упрощенная схема внутренней системы управления сервопривода}
    \label{fig:upr_servo}
\end{figure}

Положим, что при смене конфигурации конечности угловая скорость сервоприводов постоянна, т.е. углы поворота меняются по линейному закону. Также учтем, что угловыми скоростями сервоприводов невозможно управлять <<извне>>, скорость задается встроенным в сервопривод микроконтроллером (рисунок \ref{fig:upr_servo}). Тогда чем меньше точек мы берем на траектории, тем менее точно конечность описывает нужную нам кривую, что наглядно показано на иллюстрации \ref{fig:traj2}, там мы берем всего четыре точки.

\begin{figure}[h]
    \centering
    
    \caption{Моделирование движения между четырьмя точками траектории}
    \label{fig:traj2}
\end{figure}

\begin{figure}[h!]
    \centering
    
    \caption{Моделирование движения между восьмью точками траектории}
    \label{fig:traj3}
\end{figure}

Увеличение частоты точек в два раза показало гораздо лучший результат, что можно видеть на рисунке \ref{fig:traj3}. Нижняя часть траектории описана с минимальной ошибкой. Отклонение от движения по верхней части траектории все еще сохраняется, но уже является допустимым при применении на практике.

В прототипе на данном этапе разработки применен именно этот способ движения ног.

\section{Замечание о проблеме выбора оптимальной траектории}

Эллипс не является оптимальной траекторией для описания движения конечности при ходьбе. В идеале, роботам требуются более сложные траектории. Причем в них нужно вносить коррективы при любых изменениях в механике робота. Данная сложность была решена при помощи искусственных нейронных сетей \cite{Singla2018}. Обученные модели могут помочь разработчикам найти сложные оптимальные траектории движения для ног робота. К сожалению, входной порог для изучения и последующего применения таких моделей очень высок, поэтому они не были применены при разработке прототипа.

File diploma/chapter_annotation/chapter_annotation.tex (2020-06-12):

\likechapter{Аннотация}

В рамках работы рассматривается разработка шагающего четырехногого робота с упором на проблему разработки конечностей и программирования. Спроектированы трёхмерные твердотельные чертежи системы, собрана физическая модель. Обоснован выбор конструктивных решений, выбор программной архитектуры, выбор алгоритмов. Применены лучшие практики работы с кодом, разработаны программные библиотеки для управления микроконтроллерами в составе робота.

% Спроектированы драйверы для бесколлекторных двигателей, позволяющие осуществлять точное позиционирование трёхфазного бесколлекторного двигателя. Исследована механика системы в "стоячем" режиме. 

% Построена трёхмерная твердотельная модель системы и проведена её физическая симуляция, обучение ходьбе. Обученная в симуляции модель применена к настоящей физической модели робота. Спроектирована и запрограммирована система управления.

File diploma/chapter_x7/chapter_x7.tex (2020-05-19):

\chapter{\MakeUppercase{Механическая конструкция}}
\section{Проектирование ног}
Основная, и самая сложная с точки зрения механики часть шагающего робота, это конечности. Как и корпус, ноги проектировались в виде трёхмерных, твердотельных чертежей. Для уменьшения количества уникальных деталей конструкция всех четырех ног была унифицирована. Таким образом снижена сложность и затратность в производстве деталей. 

Сложные по форме детали изготовлены из пластика на 3D-принтере, в конструкции также присутствуют металлические стержни, стандартные металлические кронштейны, крепежные элементы (винты, гайки).

Перед проектированием были выдвинуты функциональные требования к конечностям. Они должны быть как можно менее габаритными, для сохранности редукторов сервоприводов и для увеличения скорости движения нужно максимально уменьшить момент инерции конечности. Основной способ достижения этой цели -- уменьшение веса всех деталей. Поэтому крепежные и элементы корпуса, были изготовлены из пластика, там где это было возможно. Были использованы полые цилиндрические аллюминиевые трубки в качестве стержней, обеспечивающих жесткость.

Есть еще один, не менее эффективный способ снизить момент инерции ног, не уменьшая общего веса конечностей -- концентрация основной массы как можно выше, ближе к месту крепления ноги к корпусу. Поэтому сервоприводы, как одни из самых тяжелых элементов конструкции, были перенесены максимально близко к корпусу и максимально далеко от пола.

В связи с этим в конструкции возник механический четырехзвенник, позволяющий для вращения последнего звена ноги установить сервопривод не непосредственно в шарнир, а передать вращение двигателя издалека. Четырехзвенник усложнил кинематическую схему ноги, его расчет рассмотрен далее, однако такая конструкция не только хорошо повлияла на механические характеристики ноги, но и на эстетические тоже. Крутящий момент передается при помощи кинематического четырехзвенника и двигатель, который имеет неоптимальные габариты, не пришлось размещать в последнем узле ноги, что позволило сделать конечность максимально компактной.

В конструкции предусмотрена установка датчиков касания на стопы, в ходе развития проекта. Стопы можно будет заменить на более совершенные, а конструкция ноги позволит без проблем проложить провода внутри стержней, либо сокрытыми за стенками корпуса.

Из-за специфики сервоприводов возникают проблемы во время сборки, которые замедляют процесс сборки и требуют наличия управляющей электроники. Дело в том что при установке в конструкцию ноги, сервопривод должен быть верно сконфигурирован, или проще говоря, быть заранее повернутым на известный далее управляющей программе угол поворота. Так называемый технический угол. Этим минусом обладают все сервоприводы такого типа. В других видах приводов конфигурировать углы поворота при сборке не нужно, но каждый раз при запуске нужно калибровать приводы, поворачивая их в нулевое, начальное положение. Такие приводы не были использованы в силу своей дороговизны и в силу того что наличие концевых выключателей в конструкции конечности сильно бы усложнило разработку. Для прототипа это излишне.

\section{Проектирование корпуса}

\section{Подбор комплектующих}
\subsection{Статические детали}

\subsection{Силовая электроника}

\subsection{Логическая электроника}

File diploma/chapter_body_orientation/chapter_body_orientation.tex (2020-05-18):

\chapter{\MakeUppercase{Ориентация тела робота}}
\section{Кватернионы}

\section{Произвольные повороты тела в пространстве}

\section{Связь ориентации тела с конфигурацией ног}

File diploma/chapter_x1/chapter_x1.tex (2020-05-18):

\chapter{\MakeUppercase{Шагающие роботы}}

\section{Задачи работы}

В рамках работы рассматривается разработка шагающего четырехногого робота, с упором на проблему разработки конечностей, подбора электроприводов и их управления. Сравниваться будут два типа электроприводов: заводские микро-сервоприводы с редуктором и бесколлекторные синхронные двигатели (BLDC). 

Требуется:
\begin{itemize}
    \item Рассчитать худший (по нагрузке) статический случай для конечностей 4-х ногого робота.
    \item Подобрать два электропривода удовлетворяющих по крутящему моменту. Для двух типов электроприводов разработать модель конечностей.
    \item Собрать физическую модель конечностей двух типов.
    \item Сравнить управляемость и механические характеристики конечностей двух типов.
    \item Применить самую удачную конструкцию конечностей при сборке робота.
    \item Запрограммировать управление робота.
\end{itemize}

\section{Актуальность работы}

Задача разработки конечностей для шагающих роботов настолько же важная, как и задача навигации роботов. Сегодня она актуальна, как никогда ранее. Всё в большей степени людей стараются заменять шагающими роботами для работ вроде общего тех. осмотра помещений, исследования местности вдали от дорог и цивилизации, помощи в устранении последствий катастроф. Открытость методик, исходных кодов и готовых рассчитанных моделей приведет к массовой разработке шагающих роботов не только крупными предприятиями, но и мелкими разработчиками.

\section{Анализ}

Для поставленных ранее задач можно сформировать последовательность действий, которые приведут к их решению.

\subsection{Рассчёт худшего статического случая}

«Худшим» случаем называется такой, при котором одному или нескольким приводам нужно приложить максимальный момент для поворота звена конечности в нужную сторону.

Для того чтобы определить худший случай, нужно вообще определиться с кинематикой конечности. Оптимальной кинематикой можно считать конечность с 3 степенями свободы:

\begin{figure}[ht]
    \centering
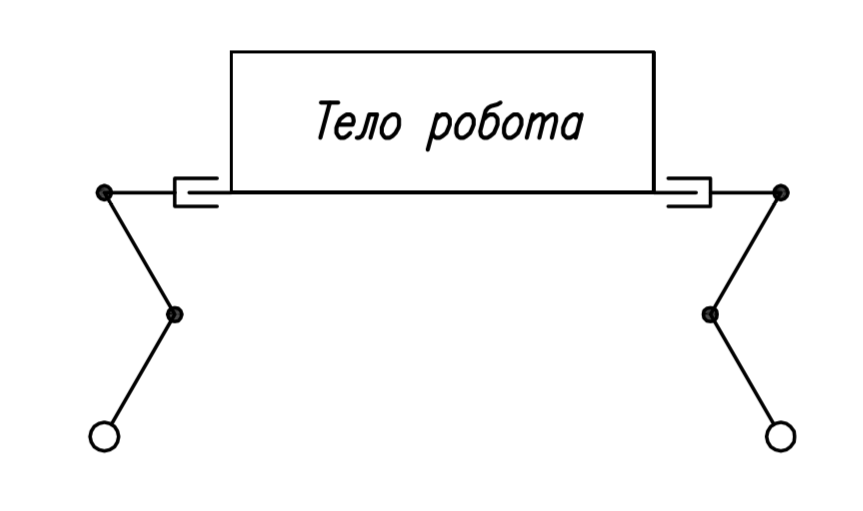
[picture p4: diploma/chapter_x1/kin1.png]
    
    \caption{Кинематика 4-х ногого робота, вид сбоку}
\end{figure}

Худшим случаем считается случай, в котором робот лежит на «животе» с выпрямленной конечностью. Чтобы подогнуть под себя конечность, нужно будет преодолеть момент $M_{худш}$ с учетом массы тела робота $m$.

\begin{figure}[ht]
    \centering
    
    \caption{Кинематика 4-х ногого робота, вид сбоку (худший случай)}
\end{figure}

При расчёте в первом приближении можно пренебречь трением и весами звеньев. Также можно учесть, что нагрузка, создаваемая массой тела робота будет распределена равномерно по всем 4-м ногам. Это значит что на одну ногу будет приходится лишь $\frac{1}{4}m$ тела робота.

Также, в первом приближении допустим, что тело робота может достигать 2-х килограмм. Большая часть веса придется на каркас конструкции, собранный из пластика. Меньшая часть веса придется на аккумулятор. Еще более маленькая часть придется на проводку и крепежи. Самыми легкими составляющими конструкции окажутся электронные компоненты.

При таком расчете можно считать что каждой ноге надо будет «поднять» около 0.25 кг веса. Тогда в худшем случае, приложенный момент вычисляется просто:
$$ M_{худш}=(l_{1}+l_{2}) m g, $$
\noindent здесь $l_1$ и $l_2$ - длины звеньев.

Мы можем подобрать длины звеньев таким образом, чтобы они обеспечивали достаточную для задач ходьбы рабочую область и одновременно наименьший требуемый момент. Однако сначала нам нужно будет измерить реальные моменты на подобранных электроприводах.

\subsection{Подбор электроприводов}

Исходя из ожидаемых моментов и скоростей были выбраны два вида электроприводов:

\begin{itemize}
    \item Заводской сервопривод DSSERVO RDS3225
    \item BLDC-мотор DYS BGM5208-200-12
\end{itemize}

Использовать паспортные данные двигателей для расчётов нельзя, нужно измерить их реальный момент вращения. Для измерения крутящих моментов были разработаны стенды, принцип действия которых можно описать следующей схемой:

\begin{figure}[ht]
    \centering
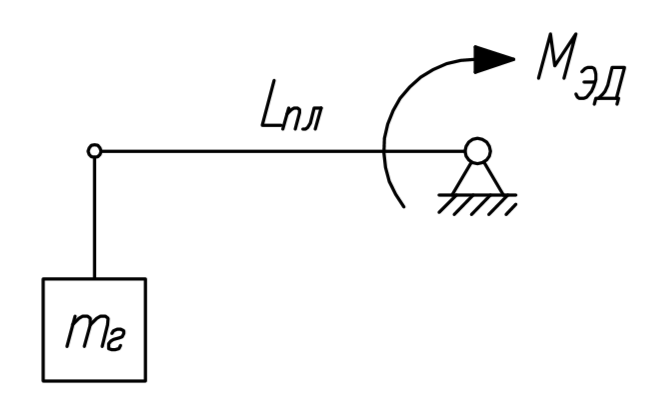
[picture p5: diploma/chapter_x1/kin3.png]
    
    \caption{Кинематика стенда для измерения крутящего момента}
\end{figure}

На изображении $ m_г $ - масса груза, которая нам известна, и которую мы можем менять. $ L_{пл} $ - длина плеча, также известная нам. Из приведенных величин можно легко найти экспериментально значение момента $ M_ {ЭД} $.

Чертеж стенда для BLDC двигателя:

\begin{figure}[ht]
    \centering
    % левая картинка
    \begin{subfigure}[b]{0.45\textwidth}    
        \centering
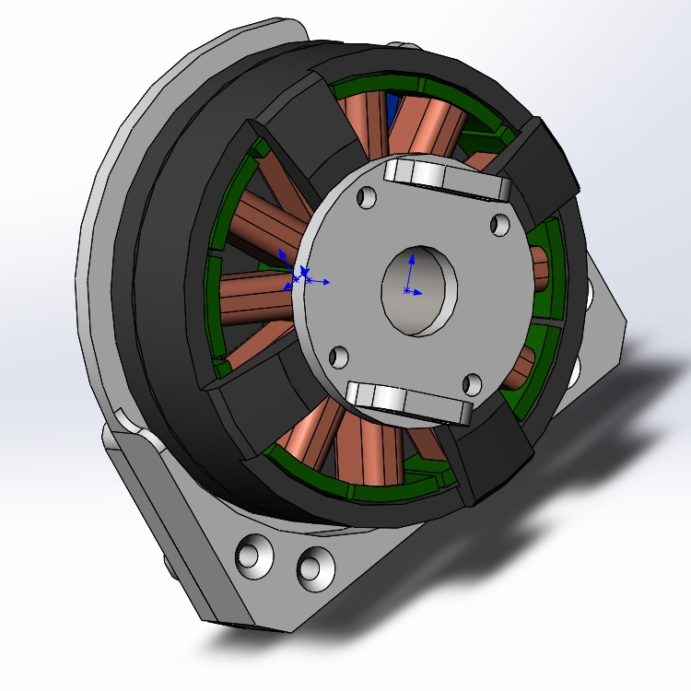
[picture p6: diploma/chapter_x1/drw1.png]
        
        \caption{}
    \end{subfigure}
    % правая картинка  
    \begin{subfigure}[b]{0.45\textwidth}
        \centering
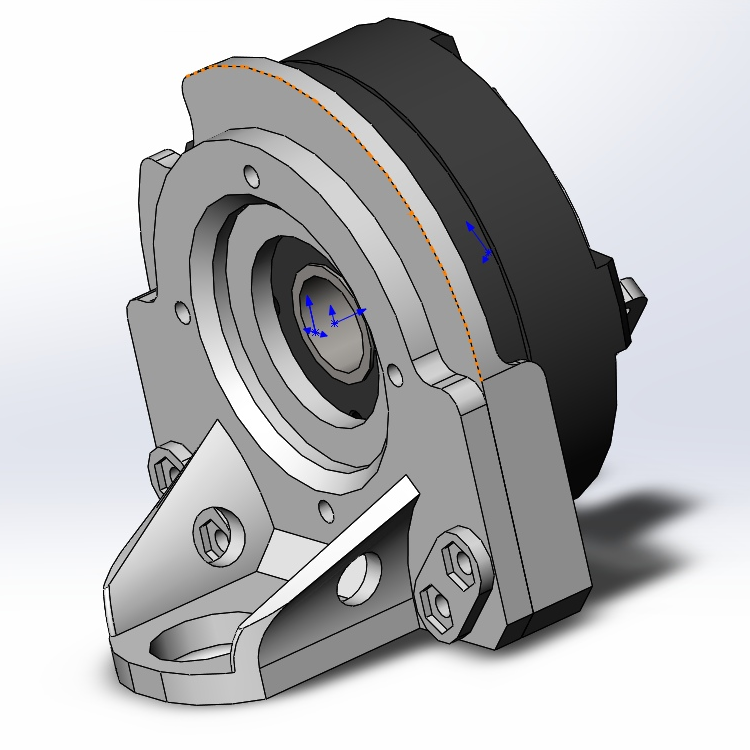
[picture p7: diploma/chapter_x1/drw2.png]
        
        \caption{}
    \end{subfigure}
     
    \caption{(a) Стенд для измерения крутяжего момента BLDC мотора, вид спереди; (б) Тот же стенд, вид сзади.}
    \label{fig_bldc_test_drawings}
\end{figure}

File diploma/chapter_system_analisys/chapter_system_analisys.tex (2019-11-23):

\chapter{\MakeUppercase{Анализ системы}}
\section{Кинематика ходьбы}

Верхняя его часть \textit{антропоморфна}, однако ног у него четыре, что выделяет его на фоне роботов антропоморфной конструкции в вопросах мобильности и устойчивости. \cite{Hwangbo2019} Стоит отметить, что данный аппарат не полностью автономен, и для полноценной работы ему потребуется оператор, однако по словам разработчиков в случае, например, обрыва питания робот может продолжить выполнение задач самостоятельно. 

\section{Динамика ходьбы}

Каждая нога состоит из манипулятора с четырьмя степенями свободы (поворот в плоскости платформы, и три поворота в вертикальной плоскости) и колеса, имеющего две степени свободы относительно конечного звена манипулятора. \cite{Seok2012}

\begin{figure}[ht]
    \centering
        \begin{subfigure}[b]{0.3\textwidth}
        \centering
            $$\begin{array}{l}
            F \to x \;|\; y \;|\; (S) \\
            T \to F \;|\; T \ast F \\
            S \to T \;|\; S + T \\    
            \end{array}$$
            \caption{}
        \end{subfigure} %    
        \begin{subfigure}[b]{0.6\textwidth}
        \centering
            %\includegraphics[scale=0.7]{parseTree.png}
            $$\begin{array}{l}
            F \to x \;|\; y \;|\; (S) \\
            T \to F \;|\; T \ast F \\
            S \to T \;|\; S + T \\    
            \end{array}$$
            \caption{}
        \end{subfigure}
        
        \caption{(a) Продукции грамматики $G$ для порождения арифметических выражений; 
                    (б) Дерево разбора строки $x+y\ast y$ в грамматике $G$.}
        
        \label{fig_parsetree}
    \end{figure}

    \begin{table}[ht]
        \caption{Расчет весомости параметров ПП}
        \label{tab_weight}
        \centering
            \begin{tabular}{|c|c|c|c|c|c|c|c|c|}
            \hline \multirow{2}{*}{Параметр $x_i$} & \multicolumn{4}{c|}{Параметр $x_j$} & 
                \multicolumn{2}{c|}{Первый шаг} & \multicolumn{2}{c|}{Второй шаг} \\
            \cline{2-9} & $X_1$ & $X_2$ & $X_3$ & $X_4$ & $w_i$ & 
                ${K_\text{в}}_i$ & $w_i$ & ${K_\text{в}}_i$ \\
            \hline $X_1$ & 1 & 1 & 1.5 & 1.5 & 5 & 0.31 & 19 & 0.32 \\
            \hline $X_2$ & 1 & 1 & 1.5 & 1.5 & 5 & 0.31 & 19 & 0.32 \\
            \hline $X_3$ & 0.5 & 0.5 & 1 & 0.5 & 2.5 & 0.16 & 9.25 & 0.16 \\
            \hline $X_4$ & 0.5 & 0.5 & 1.5 & 1 & 3.5 & 0.22 & 12.25 & 0.20 \\
            \hline \multicolumn{5}{|c|}{Итого:} & 16 & 1 & 59.5 & 1 \\
            \hline
            \end{tabular}
    \end{table}

    \begin{equation}
        \begin{bmatrix}
            a & b \\ c & d
        \end{bmatrix}
    \end{equation}

%     \begin{python}
% import clapi as api
% api.start() # hehehe
%         \end{python}

%         \begin{cpp}
% int main() {
%     printf("hello world")
%     return 0;
% }
%         \end{cpp}

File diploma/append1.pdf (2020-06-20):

ПРИЛОЖЕНИЕ А
Построение рабочей области Длины звеньев:
a0 = 0;
a1 = 46.22 * 10-3;
a2 = 20.02 * 10-3;
a3 = 44 * 10-3;
a4 = 20.02 * 10-3;
a5 = 27 * 10-3;
a6 = 87 * 10-3;
a7 = 107 * 10-3;
a8 = 12.62 * 10-3;
a9 = 24.5 * 10-3;
a10 = 110 * 10-3 - a9;

Уравнения прямой кинематики:
In[216]:= XA = a2 + a3

косинус

Cos[φ2] + a6

синус

Sin[φ2] - a8

косинус

# Cos[φ2 + φ4] + (a9 + a10)

синус

Sin[φ2 + φ4];

YA = (a1 - a3

синус

Sin[φ2] + a6

косинус

Cos[φ2] + a8

синус

# Sin[φ2 + φ4] + (a9 + a10)

косинус

# Cos[φ2 + φ4])

синус

Sin[φ1];

# ZA = -(a1 - a3

синус

Sin[φ2] + a6

косинус

Cos[φ2] + a8

синус

# Sin[φ2 + φ4] + (a9 + a10)

косинус

# Cos[φ2 + φ4])

косинус

Cos[φ1];

Четырехзвенная передача:

In[149]:= d = a5

2 + a7

2 - 2 a5 a7 Cosφ3 +

π

2

- ;
γ =

арксинус

ArcSin
a5

d косинус

Cos[φ3];
δ =

арккосинус

ArcCos
d

2 + a9

2 - a7
2

### 2 d a9

;
φ4 = (π - γ - δ);

Построение рабочей области:

In[219]:= R =

параметрический заданный геометрический регион

ParametricRegion

{XA, ZA} /. {φ1 0, φ2 phi2, φ3 phi3}, phi2,

-π

2

, 0, phi3,

-π

4

,

π

4

;

xtext =

ряд

Row[{

стиль

Style["X",

курсив

Italic], ", м"}];

ytext =

ряд

Row[{

стиль

Style["Z",

курсив

Italic], ", м"}];

пок⋯

Show[

область

Region[R],
линии коорди⋯

GridLines ->
автоматиче⋯

Automatic,
оси

Axes ->

истина

True,

точка пересечени⋯

AxesOrigin 0,

обозначения на осях

AxesLabel {xtext, ytext},

аспектное отношение

AspectRatio {1, 1},

стиль отметки

LabelStyle {

чёрный

Black,
семейство шр⋯

FontFamily "

умножить

Times",
размер шрифта

FontSize 14}]

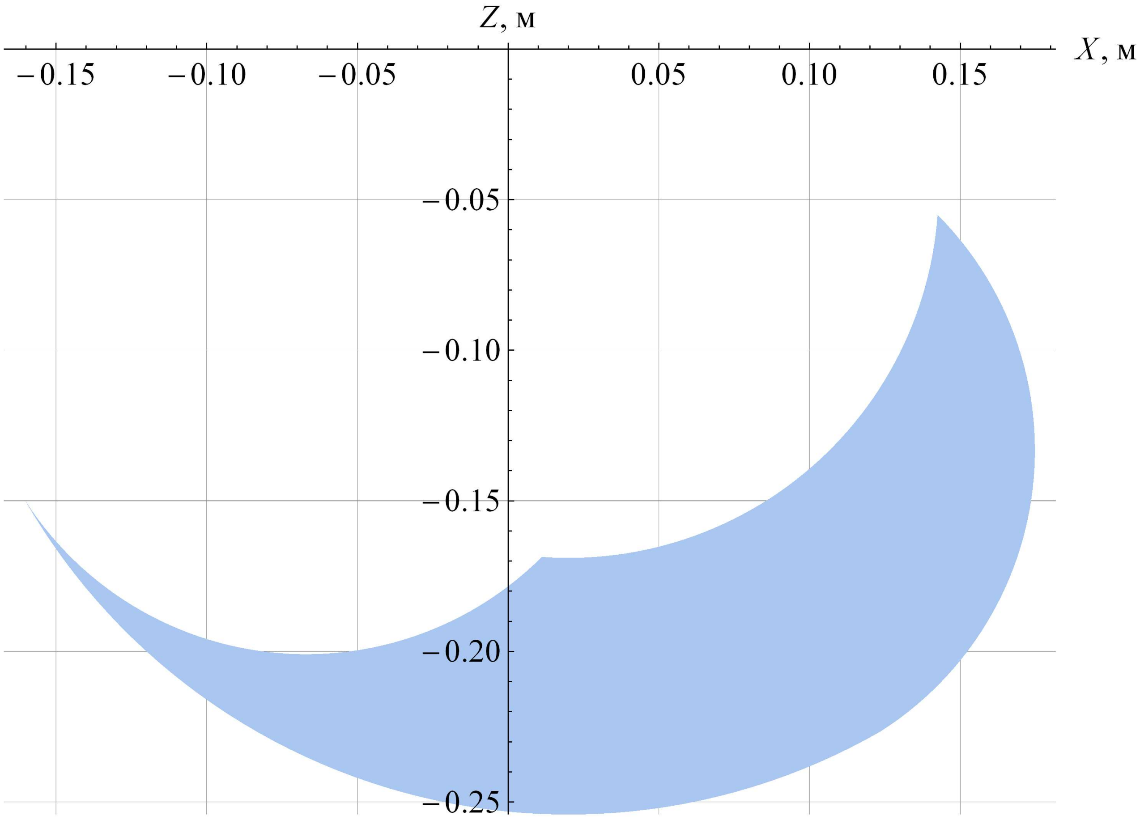
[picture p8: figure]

Out[222]=

### 2 Diploma Append A.nb

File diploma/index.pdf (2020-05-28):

## Разработка прототипа четырехногого

## шагающего робота

Коломейцев А.А.

### НИУ "МЭИ"

28 мая 2020 г.

АННОТАЦИЯ

В рамках работы рассматривается разработка шагающего четырехногого робота, с упором на проблему разработки конечностей и программирования. Спроектированы трёхмерные твердотельные чертежи системы, собрана физическая модель. Обоснован выбор конструктивных решений, выбор программной архитектуры, выбор алгоритмов. Применены лучшие практики работы с кодом, разработаны программные библиотеки для управления микроконтроллерами в составе робота.

ОГЛАВЛЕНИЕ

ГЛАВА 1 ШАГАЮЩИЕ РОБОТЫ | 6
ГЛАВА 2 МЕХАНИЧЕСКАЯ КОНСТРУКЦИЯ | 10
ГЛАВА 3 КИНЕМАТИКА КОНЕЧНОСТЕЙ РОБОТА | 18

3.5 Оптимизация численного решения обратной задачи ....... 27

ГЛАВА 4 ОРИЕНТАЦИЯ ТЕЛА РОБОТА | 30

ГЛАВА 5 МОДЕЛИРОВАНИЕ ХОДЬБЫ | 31
ГЛАВА 6 ПРОГРАММНАЯ АРХИТЕКТУРА | 32
ГЛАВА 7 ЗАКЛЮЧЕНИЕ | 39

ВВЕДЕНИЕ

Шагающие роботы - это класс роботов, имитирующих движения людей и животных. Миллионы лет эволюциии показывают, что передвижение при помощи ног это наиболее эффективный способ быстро приспосабливаться к плохим, неровным поверхностям. Люди пытались описывать ходьбу шагающими механизмами, математическими формулами. На сегодняшний день понятно, что ни один из этих двух способов к результатам, применимым на практике, не приведет. От шагающей системы требуется приспособиться к тем условиям, в которых она раньше не была.

Рынок шагающих роботов

Классифицировать шагающие машины можно не только по количеству ног. Некоторые роботы комплектуются также и колесами, для увеличения скорости передвижения по ровным поверхностям.

На текущий момент можно найти огромное количество шагающих роботов. Гексаподы, робо-пауки и т.д. Но среди сотен моделей можно выделить всего несколько роботов, ходьба которых максимально приближена к животной.

Из четырёхногих роботов лучшие результаты показывают:

- Роботы Spot и Spot-Mini от компании Boston Dynamics
- Робот Mini-Cheetah от студентов MIT
- Робот ANYmal от студентов Цюрихского университета
- Робот HyQReal от IIT (Итальянского технологического института)
- Роботы LaikaGo и AlienGo от компании Unitree Robotics

Среди двуногих можно выделить такие проекты, как:

- Робот Digit от компаний Agility Robotics и Ford
- Робот Cassie от компании Agility Robotics
- Робот Atlas от компании Boston Dynamics

Всех выше перечисленных роботов объединяет одно важное свойство -они обучены ходить. Алгоритм их ходьбы не описан статическими константами в коде, он создан при помощи методов машинного обучения. Благодаря этому все они показывают высокую степень мобильности и адаптивности к окружающей среде. Их перемещения похожи на то, как могли бы перемещаться животные со схожим механическим строением тела.

Будущее шагающих роботов именно за машинным обучением, а если быть точнее, за глубоким обучением c подкреплением (reinforcement learning). Модели, обученные в симуляции показывают более высокий КПД при перемещении [1] и меньшее потребление тока, чем модели ходьбы, описанные человеком вручную.

ГЛАВА 1

ШАГАЮЩИЕ РОБОТЫ

### 1.1 Задачи работы

В рамках работы рассматривается разработка шагающего четырехногого робота, с упором на проблему разработки конечностей и программирования.

Для выполнения работы требуется:

- Рассчитать худший (по нагрузке) статический случай для конечностей 4-х ногого робота.
- Подобрать электроприводы удовлетворяющие по крутящему моменту.
- Подобрать остальные комплектующие, входящие в состав робота и обеспечивающие его автоновную работу.
- Спроектировать и собрать физическую модель робота.
- Запрограммировать управление робота.
- Изучить управляемость и механические характеристики такого робота.

### 1.2 Актуальность работы

Задача разработки конечностей для шагающих роботов настолько же важная, как и задача навигации роботов. Сегодня она актуальна, как никогда ранее. Всё в большей степени людей стараются заменять шагающими роботами для работ, в которых требуется мобильность и подвижность человеческих ног, и при этом невозможно присутствие самого человека. Речь о работах вроде общего тех. осмотра помещений, исследования местности вдали от дорог и цивилизации, помощи в устранении последствий катастроф, пребывание в опасной для человека среде (под поздействием вредных газов, излучения). Открытость методик, исходных кодов и готовых моделей в открытом доступе приведет к массовой разработке шагающих роботов не только крупными предприятиями, но и мелкими разработчиками.

### 1.3 Анализ

Для поставленных ранее задач можно сформировать последовательность действий для дальнейшей работы. Хотя изначально данных было недостаточно, исходя из опыта были сделаны некоторые предположения по требуемым габаритам конечностей робота и крутящим моментам двигателей, которые в последствии оказались верны.

Далее исходя из дополненных данных о длинах и моментах нужно лишь рассчитать ограничение на массу тела робота, после чего можно продолжать работу.

### 1.3.1 Рассчёт худшего статического случая

«Худшим» случаем называется такой, при котором одному или нескольким приводам нужно приложить максимальный момент для поворота звена конечности в нужную сторону.

Для того чтобы определить худший случай, нужно вообще определиться с кинематикой конечности. Оптимальной кинематикой можно считать конечность с 3 степенями свободы:


Рисунок 1.1 — Кинематика 4-х ногого робота, вид сбоку

Худшим случаем считается случай, в котором робот лежит на «животе» с выпрямленной конечностью. Чтобы подогнуть под себя конечность, нужно будет преодолеть момент Mхудш с учетом массы тела робота m.

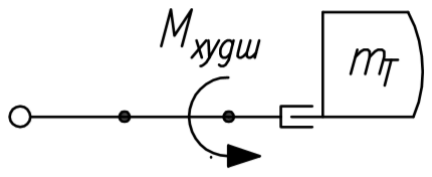
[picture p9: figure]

Рисунок 1.2 — Кинематика 4-х ногого робота, вид сбоку (худший случай)

При расчёте в первом приближении можно пренебречь трением и весами звеньев. Также можно учесть, что нагрузка, создаваемая массой тела робота будет распределена равномерно по всем 4-м ногам. Это значит что на одну ногу будет приходится лишь 1
4m тела робота.

Также, в первом приближении допустим, что тело робота может достигать 2-х килограмм. Большая часть веса придется на каркас конструкции, собранный из пластика. Меньшая часть веса придется на аккумулятор. Еще более маленькая часть придется на проводку и крепежи. Самыми легкими составляющими конструкции окажутся электронные компоненты.

При таком расчете можно считать что каждой ноге надо будет «поднять» около 0.25 кг веса. Тогда в худшем случае, приложенный момент вычисляется просто:

Mхудш =

1
4

(l1 + l2)mg,

здесь l1 и l2 - длины звеньев.

Мы можем подобрать длины звеньев таким образом, чтобы они обеспечивали достаточную для задач ходьбы рабочую область и одновременно наименьший требуемый момент.

Спроектированные для прототипа конечности имеют характеристики:

l1 ≈ (44 + 87) × 10⁻³ = 131 мм

l2 ≈ 134.5 × 10⁻³ = 134.5 мм

С использованием приводов с крутящим моментом 2.5Н максимально допустимый вес робота будет примерно равен 3.8 кг. Такое требование к весу, с учетом изготовления деталей из аллюминия и пластика, вполне выполнимо.

### 1.3.2 Подбор электроприводов

Исходя из ожидаемых моментов и скоростей был выбран заводской сервопривод DSSERVO RDS3225.

Использовать паспортные данные двигателей для расчётов может быть рискованно, нужно измерить их реальный момент вращения. Для измерения крутящих моментов были разработаны стенды, принцип действия которых можно описать следующей схемой:


Рисунок 1.3 — Кинематика стенда для измерения крутящего момента

На изображении mг - масса груза, которая нам известна, и которую мы можем менять. Lпл - длина плеча, также известная нам. Из приведенных величин можно легко найти экспериментально значение момента MЭД. После проверки сервопривода на стенде, оказалось что действительная величина крутящего момента соответствует паспортным данным в пределах погрешности измерений.

ГЛАВА 2

МЕХАНИЧЕСКАЯ КОНСТРУКЦИЯ

### 2.1 Проектирование ног

Основная, и самая сложная с точки зрения механики часть шагающего робота, это конечности. Как и корпус, ноги проектировались в виде трёхмерных, твердотельных чертежей. Для уменьшения количества уникальных деталей конструкция всех четырех ног была унифицирована. Таким образом снижена сложность и затратность в производстве деталей.

Сложные по форме детали изготовлены из пластика на 3D-принтере, в конструкции также присутствуют металлические стержни, стандартные металлические кронштейны, крепежные элементы (винты, гайки).

Перед проектированием были выдвинуты функциональные требования к конечностям. Они должны быть как можно менее габаритными, для сохранности редукторов сервоприводов и для увеличения скорости движения нужно максимально уменьшить момент инерции конечности. Основной способ достижения этой цели – уменьшение веса всех деталей. Поэтому крепежные и элементы корпуса, были изготовлены из пластика, там где это было возможно. Были использованы полые цилиндрические аллюминиевые трубки в качестве стержней, обеспечивающих жесткость.

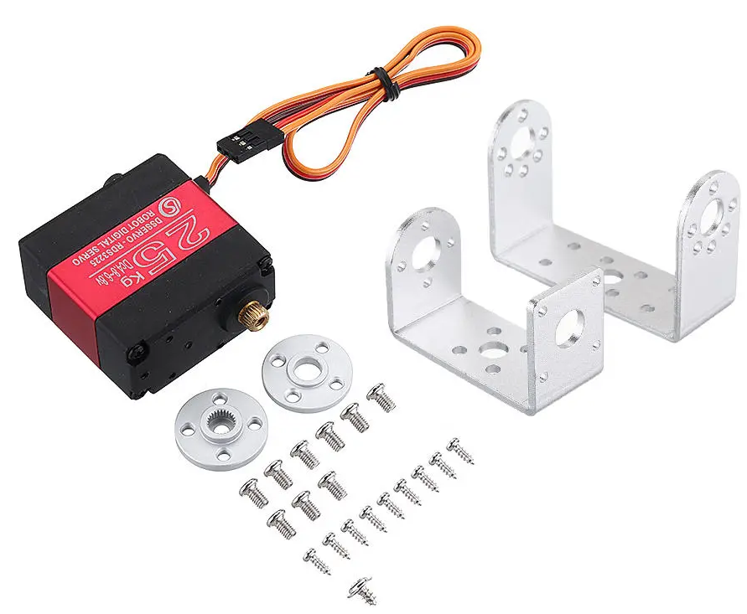
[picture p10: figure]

Рисунок 2.1 — Сервоприводы DSSERVO RDS3225, использованные в прототипе робота

Есть еще один, не менее эффективный способ снизить момент инерции ног, не уменьшая общего веса конечностей – концентрация основной массы как можно выше [2], ближе к месту крепления ноги к корпусу. Поэтому сервоприводы, как одни из самых тяжелых элементов конструкции, были перенесены максимально близко к корпусу и максимально далеко от пола.

В связи с этим в конструкции возник механический четырехзвенник, позволяющий для вращения последнего звена ноги установить сервопривод не непосредственно в шарнир, а передать вращение двигателя издалека. Четырехзвенник усложнил кинематическую схему ноги, его расчет рассмотрен далее в пункте 3.2, однако такая конструкция не только хорошо повлияла на механические характеристики ноги, но и на эстетические тоже. Крутящий момент передается при помощи кинематического четырехзвенника и двигатель, который имеет неоптимальные габариты, не пришлось размещать в последнем узле ноги, что позволило сделать конечность максимально компактной.

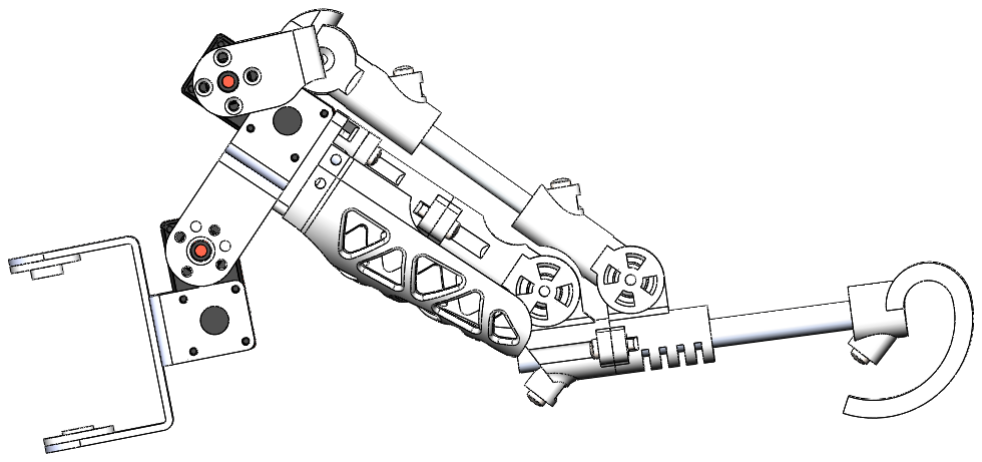
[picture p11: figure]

Рисунок 2.2 — Твердотельный чертеж конечности робота. Можно заметить что двигатели размещены у основания конечности.

В конструкции предусмотрена установка датчиков касания на стопы, в ходе развития проекта. Стопы можно будет заменить на более совершенные, а конструкция ноги позволит без проблем проложить провода внутри стержней, либо сокрытыми за стенками корпуса.

Из-за специфики сервоприводов возникают проблемы во время сборки, которые замедляют процесс сборки и требуют наличия управляющей электроники. Дело в том что при установке в конструкцию ноги, сервопривод должен быть верно сконфигурирован, или проще говоря, быть заранее повернутым на известный далее управляющей программе угол поворота. Так называемый технический угол. Этим минусом обладают все сервоприводы такого типа. В других видах приводов конфигурировать углы поворота при сборке не нужно, но каждый раз при запуске нужно калибровать приводы, поворачивая их в нулевое, начальное положение. Такие приводы не были использованы в силу своей дороговизны и в силу того что наличие концевых выключателей в конструкции конечности сильно бы усложнило разработку. Для прототипа это излишне.

### 2.2 Проектирование корпуса

Требования к корпусу можно разделить на три составляющие: массовые, габаритные и эстетические. Снижать массу нужно для того чтобы разгрузить конечности робота, защитить редукторы электроприводов. Снижению массы способствует максимальный отказ от металлических деталей, а там где это невозможно (в силу требований по жесткости), нужно использовать эффективные сечения профилей, желательно из аллюминия.

В качестве каркаса, к которому крепятся ноги робота был выбран конструкционный аллюминиевый профиль, из-за его легкости, жесткости и простоты крепления новых деталей к профилю.

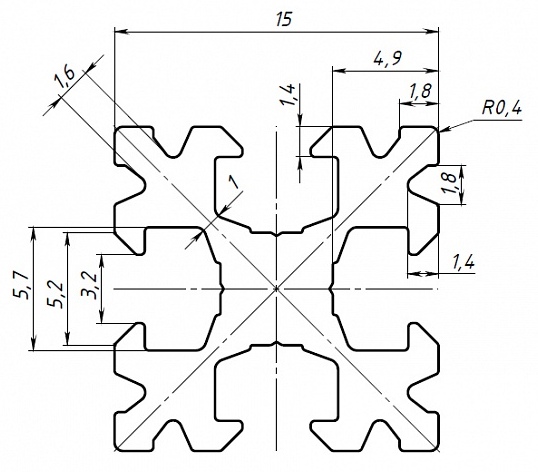
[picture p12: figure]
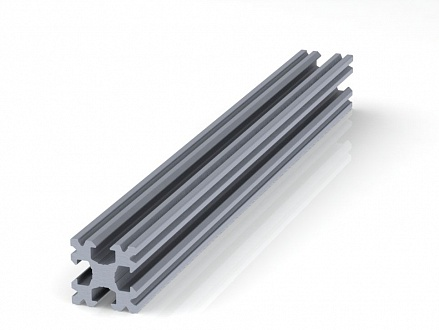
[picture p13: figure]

(а) Сечение профиля | (б) Внешний вид профиля

Рисунок 2.3 — Конструкционный аллюминиевый профиль

Объем корпусу придают тонкие цилиндрические аллюминиевые стержни, в узлах пластиковые крепежи. Такая конструкция позволяет использовать максимально много места внутри корпуса, что упрощает размещение электронных компонентов внутри. FIXME НУЖНА ИЛЛЮСТРАЦИЯ

Самой сложной задачей была компоновка всех компонентов внутри корпуса, так как нужно сохранить их «доступность» в любой момент времени для замены или диагностики. Таким образом повышается общая ремонтопригодность прототипа, а это сильно ускоряет работу с ним.

### 2.3 Подбор комплектующих

### 2.3.1 Силовая электроника

Из силовой электроники в роботе присутствуют:

- Сервоприводы
- DC-DC преобразователи напряжения.

Про подбор сервоприводов рассказано в пункте 1.3.2. Преобразователи напряжения используются максимально компактные и простые в настройке. В основном используются испульсные преобразователи на базе микросхем LM-XXXX и XL-XXXX. Они хорошо взаимозаменяемы друг с другом. Для двух пар ног выбраны два преобразователя с максимальным током нагрузки 5 А. Для питания логической части используется преобразователь с током нагрузки 3 А.

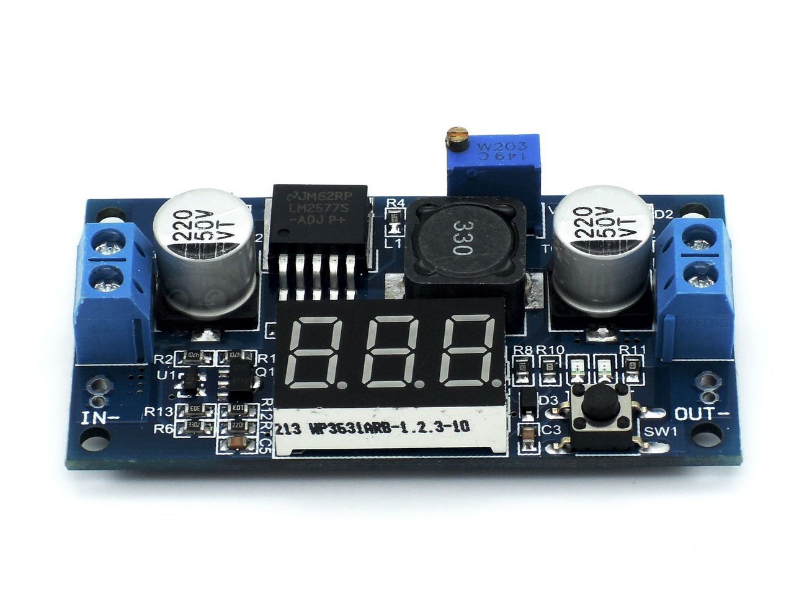
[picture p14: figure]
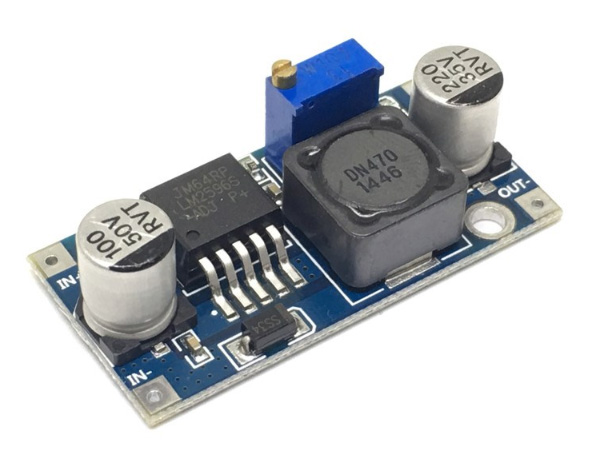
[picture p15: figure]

(а) Преобразователь на базе LM2596S (б) Преобразователь на базе LM2577

Рисунок 2.4 — Некоторая силовая электроника в составе робота

### 2.3.2 Логическая электроника

В качестве управляющего микрокомпьютера выступает Raspberry Pi 3B+. Этого достаточно для совершения множества матричных операций в секунду и для эффективной работы с высокоуровневыми абстракциями в коде.

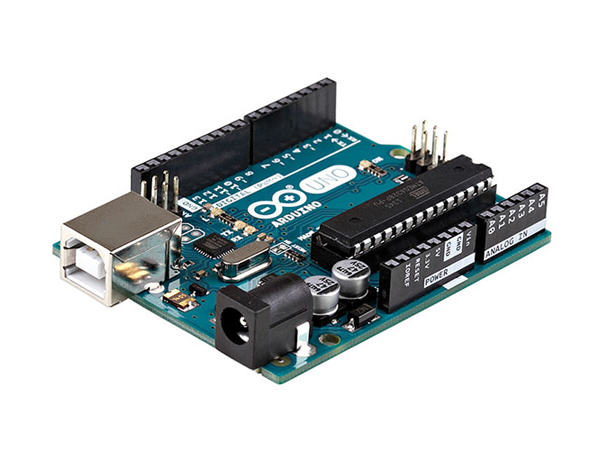
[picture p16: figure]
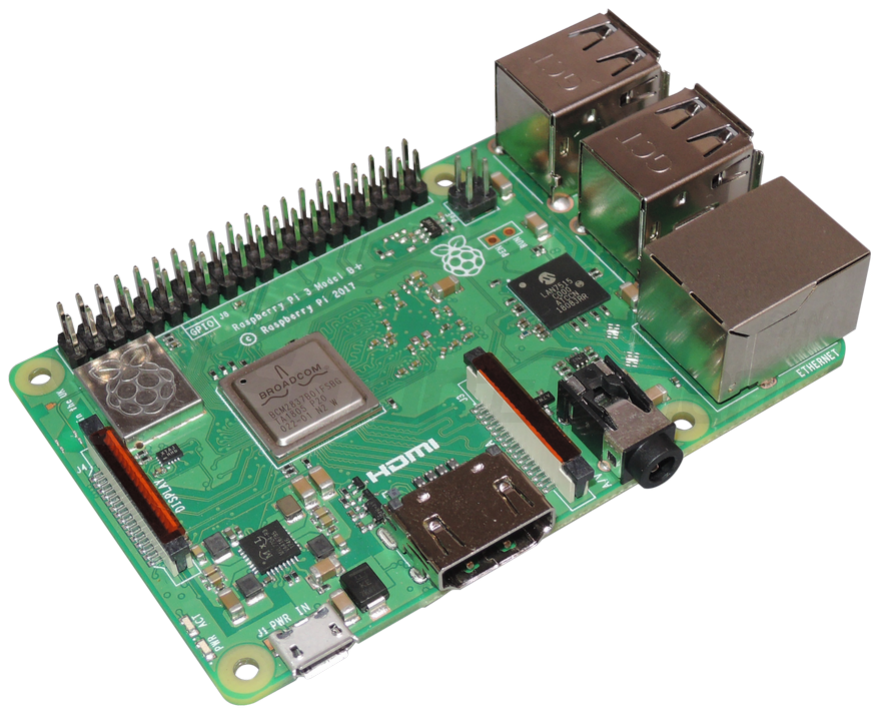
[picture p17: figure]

(а) Arduino Uno | (б) Raspberry Pi 3B+

Рисунок 2.5 — Логическая электроника в составе робота

Raspberry Pi выступает исключительно как своеобразный модуль для высокоуровневых вычислений и не работает с «железом» напрямую. Вместо этого происходит отправка команд на микроконтроллер в составе платформы Arduino. Команды формируются и передаются в цифровом виде на микроконтроллер. Сделано это по двум причинам:

- Отделение логики вычислений состояния робота от самого процесса управления.
- Электрическая защита дорогостоящего микрокомпьютера от возможных скачков тока в цепи силовой электроники.

О протоколе передачи данных и способе формирования команд подробнее написано в пункте 6.2.

### 2.4 Аккумулятор

В качестве аккумулятора был использован Литий-полимерный аккумулятор (Li-Po аккумулятор). Преимущества такого выбора приведены ниже:

- Высокая токоотдача

- Большая емкость
- Быстрая зарядка
- Наличие дешевой электроники для контроля разряда таких аккумуляторов
- Малый вес и габариты

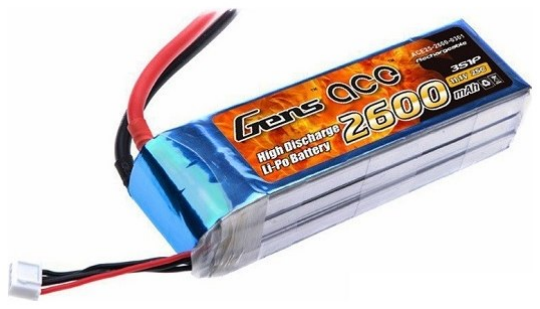
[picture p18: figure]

Рисунок 2.6 — Li-Po аккумулятор на 2600 мА·ч

С такими большими плюсами существуют и минусы, которые стоит принимать во внимание при эксплуатации такого типа аккумуляторов:

- Высокая токоотдача повышает риск получить травму при работе
- Высоки шансы на сгорание питающейся от аккумулятора электроники в случае короткого замыкания
- Требуются специальные условия хранения, если аккумуляторы долгое время не используются
- Li-Po аккумуляторы взрывоопасны при неправильной эксплуатации

Из-за большего опыта работы с Li-Po аккумуляторами (несколько последних лет) и было решено использовать их.

### 2.5 Остальные детали

Пластиковые детали изготовливались на 3D-принтере методом FDM печати (послойной) из материала PET-G. Преимущества материала для данного робота описаны ниже:

- Прочность ABS
- Термостойкость ABS
- Долговечность ABS
- Не требователен к условиям печати, как PLA
- Низкая термоусадка (почти не меняет размеры при нагревании/остывании)
- Высокие ударопрочные свойства
- Возможность красить и стерилизовать
- Не токсичен

Может показаться что при изготовлени деталей на 3D-принтере последним можно придавать любую форму, но при FDM технологии печати это не так. Технология достаточно дешева и может использоваться в дешевых домашних 3D-принтерах, поэтому у нее есть свои ограничения на печать «нависающих» над печатной областью частей детали. Поэтому при проектировании деталей из пластика нужно исходить из двух принципов. Первый заключается в том чтобы не делать новой детали из пластика, если есть альтернатива в линейке деталей, который изготавливаются по ГОСТ и продаются в специализированных магазинах. Второй принцип заключается в том чтобы использовать в детали как можно меньше материала и скомпоновать ее так, чтобы при печати максимально избежать создания поддержек для нависающих частей. Всё это накладывает свои конструктивные ограничения и требует от конструктора некоторого опыта.

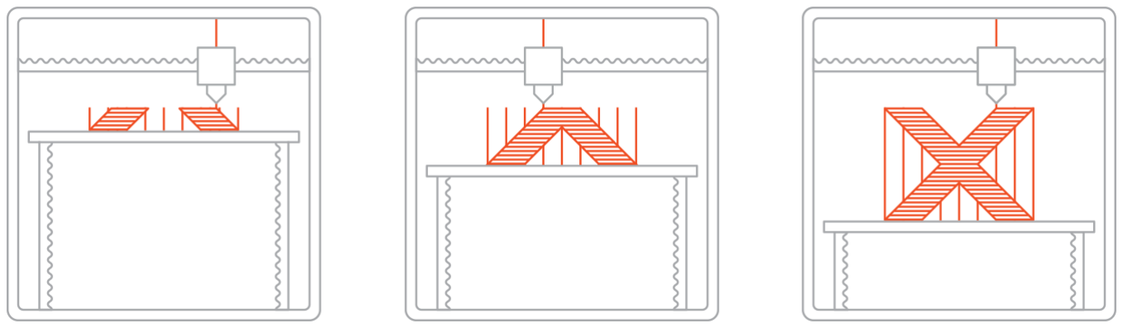
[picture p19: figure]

Рисунок 2.7 — Иллюстрация 3D-печати по технологии FDM

Из металла выполнены покупные кронштейны, стержни ног. Стержни – стандартные полые цилиндрические аллюминиевые профили. Подгонялись под нужную длину при помощи ножовки. Крепление к пластиковым узлам происходило вкручиванием в торцы стержней винтов. Такой способ приводит к хорошему зацеплению деталей.

Для того чтобы избежать разрушения пластиковых деталей в месте вкручивания винта в торец, и из-за невозможности нарезать резьбу в пластиковой детали, были использованы вставки из металлических гаек внутри пластикового материала.

ГЛАВА 3

КИНЕМАТИКА КОНЕЧНОСТЕЙ РОБОТА

### 3.1 Общее положение

Изначально планировалось, что конечность робота в общем виде будет представлять манипулятор с тремя степенями свободы. Такая конструкция множество раз рассмотрена другими людьми, существует аналитическое решение прямой и обратной задачи.

Проблема такой кинематики в механической сложности ее реализации с точки зрения конструктора. Из-за особенностей и требований, описанных в пункте 2.1, конструкция ноги получилась, как на рисунке ниже.

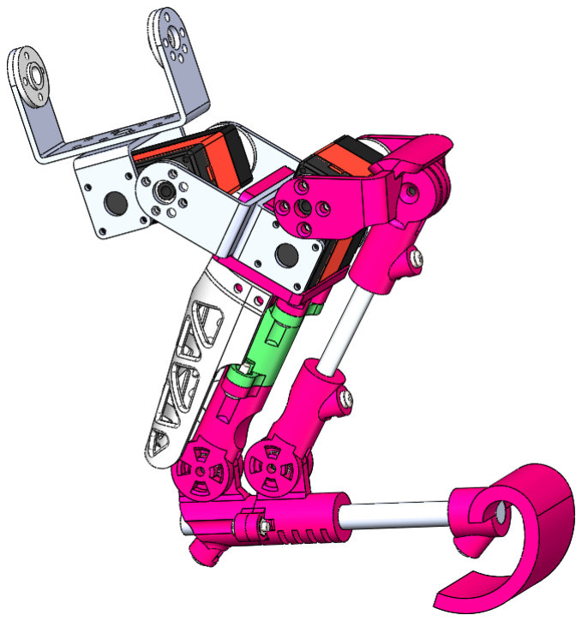
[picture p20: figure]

Рисунок 3.1 — Чертеж конструкции ноги

Для упрощения понимания ниже приведена трехмерная кинематическая схема конечности.

В составе конечности присутствует непрямой кинематический четырехзвенник (три из четырех сторон имеют разные длины). Это усложнило кинематическую задачу, сделало ее менее тривиальной. Как оказалось далее, наличие четырехзвенной передачи сделало невозможным нахождение аналитического решения обратной задачи кинематики.

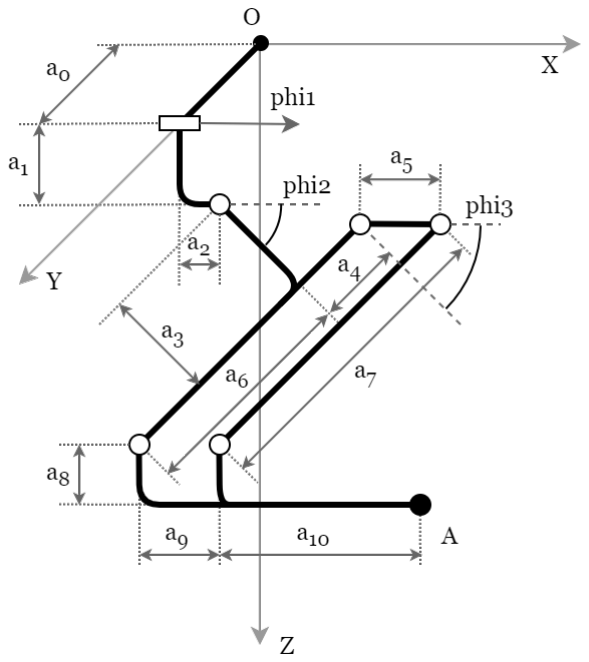
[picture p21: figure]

Рисунок 3.2 — Трехмерная кинематическая схема ноги робота

На кинематической схеме отмечены величины, численные значения которых приведены ниже:

a0 = 0.01м
a1 = 46.22 × 10⁻³м

a2 = 20 × 10⁻³м

a3 = 44 × 10⁻³м

a4 = 20 × 10⁻³м

a5 = 27 × 10⁻³м

a6 = 87 × 10⁻³м

a7 = 107 × 10⁻³м

a8 = 12.62 × 10⁻³м

a9 = 24.5 × 10⁻³м

a10 = 110 × 10⁻³м

Заметим, что расстояния a5 и a9 различаются! Диапазоны рабочих углов следующие:

φ1 = 0 . . .

π
8
φ2 = −

π
2

. . . 0

φ3 = −

π
4

π
4

Если зафиксировать первую степень свободы, φ1 = 0, тогда рабочая область ноги будет лежать в плоскости XZ. Выглядеть рабочая область с зафиксированным φ1 будет следующим образом:

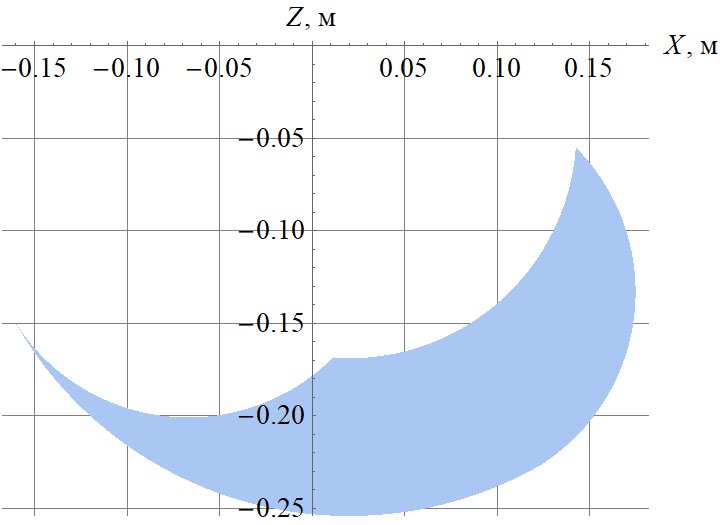
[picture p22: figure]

Рисунок 3.3 — Сечение рабочей области конечности робота

Для построения рабочей области использованы уравнения прямой кинематики, которые будут выведены в пункте 3.3.

### 3.2 Общее решение четырёхзвенника

При построении аналитического решения четырехзвенной передачи было важно подобрать функции так, чтобы для рабочих диапазонов углов φ1, φ2, φ3 не возникало переходов через ноль, или через бесконечно большие числа. Важно избежать использования кусочных функций и условных операторов для упрощения программирования. Малые диапазоны углов в рассматриваемой конечности упрощают эту задачу.

На рисунке 3.4 приведена схема четырехзвенника. Найдем зависимость φ4 от φ3. Здесь l = a4 + a6 = a7 введен для упрощения расчётных формул, т.к. две стороны четырехзвенника имеют одну длину.

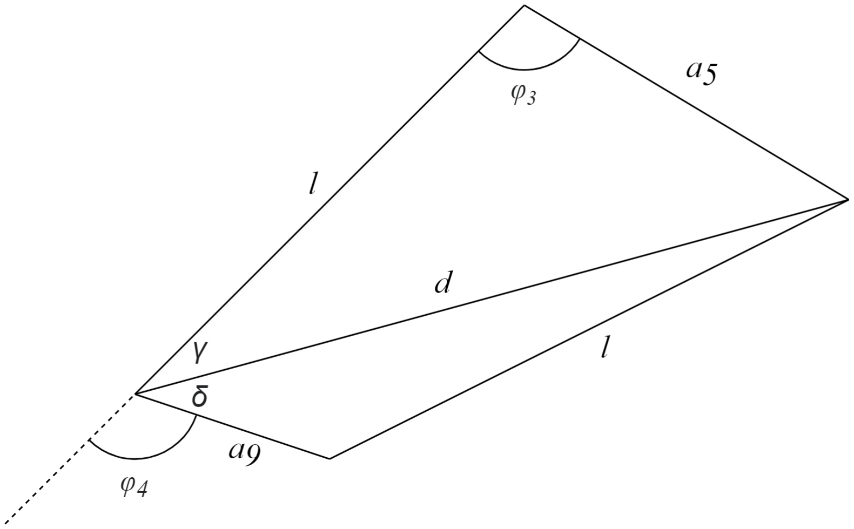
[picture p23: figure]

Рисунок 3.4 — Четырехзвенник

Сначала найдем диагональ d по теореме косинусов, для того чтобы выразить противолежащие углы:

d =

√︁
a

2
5 + l
2 − 2a5l cos(φ3) | (3.1)

С помощью уравнения 3.1 выразим углы:

γ = arcsin (︁a5
d

cos φ3

)︁
(3.2)

δ = arccos (︂
d

2 + a

2
9 − l

2
2a9l

)︂
(3.3)

И искомый угол φ4 будет находиться следующим образом:

φ4 = π − γ − δ | (3.4)

Подставим результаты 3.1, 3.2, 3.3 в уравнение 3.4 таким образом получим зависимость φ4 от φ3:

φ4 = π − arcsin (︃
√︀

a5
a

2
5 + l

2 − 2a5l cos(φ3)

cos φ3

)︃
−

− arccos (︂
a

2
5 + l

2 − 2a5l cos(φ3) + a

2
9 − l

2
2a9l

)︂
| (3.5)

### 3.3 Прямая кинематика

Используя найденную в пункте 3.2 связь построим решение прямой задачи кинематики по координатам точки A. Трехмерная кинематическая схема приведена на рисунке 3.2. Зафиксируем сначала первую степень свободы (φ1 = 0) и найдем координаты точки A в плоскости, параллельной плоскости XZ:

XA = a2 + a3 cos(φ2) + a6 sin(φ2)−

− a8 cos(φ2 + φ4) + (a9 + a10) sin(φ2 + φ4) (3.6)

ZA = a1 − a3 sin(φ2) + a6 cos(φ2)+

+ a8 sin(φ2 + φ4) + (a9 + a10) cos(φ2 + φ4) (3.7)

Если мы предположим что φ1 =

π
2

, тогда конечность будет «поднята над землей» в таком положении. Координата Z точки A станет равна нулю, координата Y увеличится. Так как от φ1 зависят только координаты Y и Z, получим следующие уравнения для координат точки A:

XA = a2 + a3 cos(φ2) + a6 sin(φ2)−

− a8 cos(φ2 + φ4) + (a9 + a10) sin(φ2 + φ4) (3.8)

YA = a0 + sin(φ1)[a1 − a3 sin(φ2) + a6 cos(φ2)+

+ a8 sin(φ2 + φ4) + (a9 + a10) cos(φ2 + φ4)] (3.9)

ZA = cos(φ1)[a1 − a3 sin(φ2) + a6 cos(φ2)+

+ a8 sin(φ2 + φ4) + (a9 + a10) cos(φ2 + φ4)] (3.10)

Таким образом прямая задача кинематики решена.

Следует отметить, что из-за того что a9 < a5, диапазон углов φ4 получился шире, чем у φ3. Это наглядно можно продемонстрировать на проекции математической модели ноги на плоскость XZ. Здесь синей точкой отмечено положение реальное положение точки A. Красной точкой отмечено положение точки A в том случае, если бы в четырехзвеннике a5 был равен a9. В крайних положениях третье звено конечности поворачивается на угол немного больший, чем поворачивается вал сервопривода.

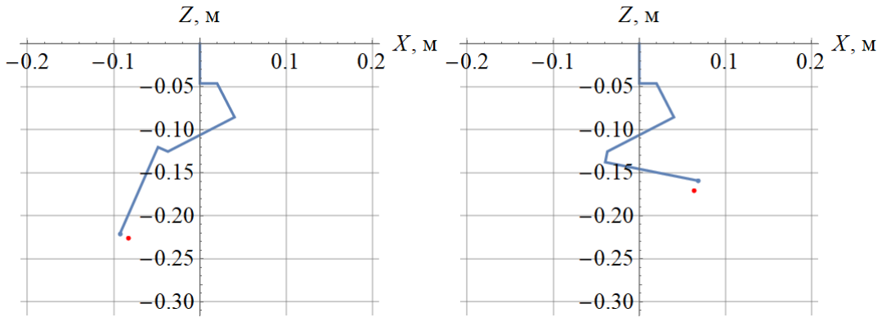
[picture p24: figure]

(а) | (б)

Рисунок 3.5 — (a) Третье звено полностью «разогнуто»; (б) Третье звено полностью «согнуто».

Таким образом за счет использования четырехзвенной передачи, увеличена рабочая область конечности. Ниже на графике зеленая область – рабочая область при a5 = a9, синяя область – расширение рабочей области при a5 > a9.

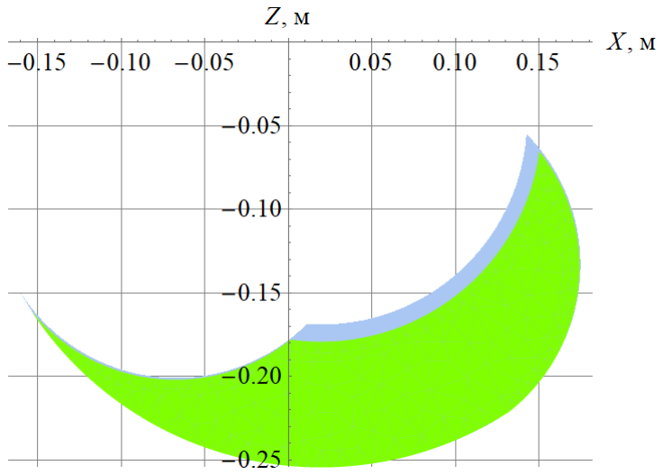
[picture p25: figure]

Рисунок 3.6 — Сравнение рабочих областей

### 3.4 Обратная кинематика

Как уже упоминалось ранее в пункте 3.1, аналитического решения для задачи обратной кинематики нет. Это значит что нужно использовать численные методы решения.

Будем искать решение с помощью метода Ньютона для систем нелинейных уравнений. В общем виде который будет выглядеть следующим образом:

Пусть дана система из n нелинейных уравнений с n неизвестными.

⎧
⎪⎪⎪⎪⎨

⎪⎪⎪⎪⎩

f1(x1, . . . , xn) = 0
f2(x1, . . . , xn) = 0
f1(x1, . . . , xn) = 0

Где fi(x1, . . . ,xn) : R

n → R, i = 1, . . . , n – нелинейные функции, определенные и непрерывно дифференцируемые в некоторой области G ⊂ R

n
. Для записи в векторном виде введем величины:

x = [x1, x2, . . . xn]

T

F(x) = [f1(x), f2(x), . . . ,fn(x)]T = 0

Нужно найти такой вектор x

* = [x

*
1

, x*
2

, . . . x*
n

]

T
, чтобы было верно равенство F(x

*
) = 0. Формула для нахождения решения итеративным методом выглядит следующим образом:

x

(k+1) = x

(k) − J

−1
(x

(k)
) × F(x

(k)
)

Где k = 1,2 . . . , а J – матрица Якоби:

J =

⎡

⎢
⎣

∂f1(x1)
∂x1

∂f1(xn)
∂xn

∂fn(x1)
∂x1

∂fn(xn)
∂xn

⎤

⎥
⎦

Применительно к задаче, рассматриваемой в данной работе, вектор x является вектором углов φ = [φ1, φ2, φ3]

T
. Вектор F(x) это правая часть уравнений прямой кинематики:

F(φ) = [XA(φ), YA(φ), ZA(φ)]T

В качестве критерия остановки итераций используется

⃦
⃦F(φ

(k)
) − F

*

⃦
⃦ < ε,
где F

*
– известное положение точки A нашего манипулятора, для которого ищутся углы звеньев.

Алгоритм поиска решения обратной задачи ниже. В нём φ

(0) – начальное

приближение, ε – точность вычислений, i – число итераций (перед выполнением алгоритма устанавливается равным нулю).

1. Расчёт Якобиана:

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
∂XA(φ1)
∂φ1

∂XA(φ2)
∂φ2

∂XA(φ3)
∂φ3

∂YA(φ1)
∂φ1

∂YA(φ2)
∂φ2

∂YA(φ3)
∂φ3

∂ZA(φ1)
∂φ1

∂ZA(φ2)
∂φ2

∂ZA(φ3)
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
2. Вычисление погрешности:

err = F(φ

(k)
) − F

*

3. Вычисление вектора полного шага:

p = J

+ × err

где J

+ – псевдо-обратная матрица Якобиана.

4. Приращение вектора полного шага к ответу:

φ

(i+1) = φ

(i) − p

5. Приращение количества итераций:

i = i + 1

6. Если заданная точность не достигнута и не превышен лимит на количество итераций, возвращаемся к пункту 1.

На практике оказалось, что скорость сходимости, и сама сходимость сильно зависит от начального приближения. После реализации алгоритма было выявлено две проблемы в его работе:

1. Невозможно подобрать такие начальные приближения, при которых бы метод сходился во всем трехмерном пространстве рабочей области.
2. В областях, в которых метод сходился в большом удалении от начального приближения, требовалось более 15 итераций для нахождения решения с заданной точностью.

Вторая проблема связана с производительностью вычислителений, которые нужно производить на микрокомпьютере в режиме реального времени.

Быстрое решение обратной задачи для любой точки трехмерной рабочей области это основное требование которое ставилось в начале разработки системы, поэтому итеративное приближение из предыдущих точек не подходит в данной ситуации. В следующем пункте приведено решение возникших проблем.

### 3.5 Оптимизация численного решения обратной задачи

Путем проб и ошибок было решено кэшировать результаты вычислений прямой кинематики во время запуска программы. Проще говоря, подготовить набор предрассчитанных начальных приближений, которые будут использоваться от момента запуска робота до момента завершения работы. Во время решения обратной задачи нужно искать в кэш-таблице ближайшее готовое решение, принимать его за начальное условие текущей задачи, и от него досчитывать более точное решение.

В качестве первой реализации две сотни предрассчитанных решений были помещены в кэш-таблицу. Каждая запись в таблице имеет две колонки. В первой колонке помещается вектор координат [XA,YA,ZA], во второй колонке вектор соответствующих им углов звеньев [φ1, φ2, φ3]. В момент поиска наилучшего начального приближения для некоторого положения конечности [X*
A

,Y *
A

,Z*
A

] находится такая запись кэш-таблицы, для которой евклидово расстояние между [X*
A

,Y *
A

,Z*
A

] и [XA,YA,ZA] будет минимально.

Простейшая реализация кэширования решений обратной кинематки:

def cache_inversed_kinematics():

global cache

cache = []
phi1_start, phi1_end = PHI1_RANGE

phi2_start, phi2_end = PHI2_RANGE

phi3_start, phi3_end = PHI3_RANGE

for phi1 in np.linspace(phi1_start, phi1_end, num=2):

for phi2 in np.linspace(phi2_start, phi2_end, num=10):

for phi3 in np.linspace(phi3_start, phi3_end, num=10):

angles = [phi1, phi2, phi3]

cache.append((direct(angles), np.array(angles)))

Пример реализации поиска решения в кэше:

def find_nearest_solution(coordinates):

global cache
return min(cache, key=lambda di: np.linalg.norm(

(coordinates - di[0]),
ord=2

))[1]

Таким образом получилось решить сразу две проблемы, описанные в пункте 3.4. Теперь на всей рабочей области обеспечена сходимость алгоритма. Поиск по кэш-таблице гораздо менее тяжеловесен чем итерации метода Ньютона, а после того как найдено «ближайшее» решение, метод Ньютона быстро досчитывает ответ в среднем за 2-3 итерации.

Таким образом реализация функции поиска решения обратной задачи выглядит так:

def inversed(coordinates):

"""
SOLVING THE INVERSE KINEMATICS PROBLEM \n

Param coordinates is [X, Y, Z] numpy vector, in meters.

This function uses Newton’s numerical method.

"""
phis = find_nearest_solution(coordinates)

error = np.ones((3,), dtype=np.float64)

i = 0
while np.linalg.norm(error, 2) > 1e-5 and i < 100:

J = jacobian(phis)

X = direct(phis)

error = X - coordinates

p = np.matmul(np.linalg.pinv(J), error)

phis = phis - p

i += 1

return phis

Пути для дополнительной оптимизации:

1. Проследить за равномерным распределением кэшированных решений в пространстве рабочей области. В случае равномерного распределения, размер кэша можно сильно уменьшить. Это ускорит поиск по таблице.
2. Уменьшать количество кэшированных решений до тех пор пока метод Ньютона продолжает быстро сходиться. Это так же позволит сократить размер кэша и увеличить скорость поиска по нему.

ГЛАВА 4

ОРИЕНТАЦИЯ ТЕЛА РОБОТА

### 4.1 Кватернионы

### 4.2 Произвольные повороты тела в пространстве

### 4.3 Связь ориентации тела с конфигурацией ног

ГЛАВА 5

МОДЕЛИРОВАНИЕ ХОДЬБЫ

### 5.1 Траектории движения ног

### 5.2 Проблема выбора оптимальной траектории

ГЛАВА 6

ПРОГРАММНАЯ АРХИТЕКТУРА

### 6.1 Структура управления

Высокоуровневая логика запрограммирована на микрокомпьютере Raspberry Pi. Тот в свою очередь отправляет последовательность команд на платформу Arduino. Последняя управляет сервоприводами через специальный драйвер
и отправляет информацию о своем состоянии в виде обратной связи обратно на микрокомпьютер.

FIXME НУЖНА ИЛЛЮСТРАЦИЯ

### 6.2 Протокол передачи данных

Отправка команд от Raspberry Pi к Arduino и последующий прием обратной связи, производится через интерфейс Serial. Это самый надежный вариант при условии, что для установки соединения используется обыкновенный USB кабель, который уже защищен от помех и штекер которого надежно закреплен в разъеме.

Для достижения наилучшей скорости реакции микроконтроллера на команды был разработан специальный протокол передачи данных и написаны легковесные программные библиотеки. Для платформы Arduino код написан на языке C++, для микрокомпьютера Raspberry Pi была разработана библиотека на языке Python.

Библиотека для передачи данных написана для трёх платформ. Она сильно упрощает наладку управления Arduino с помощью Raspberry Pi. Основная идея программного кода в том, чтобы микрокомпьютер отправлял на микроконтроллер максимально простые команды, состоящие из массива байт, в который зашифрованы лишь целочисленный номер и вещественные аргументы. Обратная связь от микроконтроллера реализована в формате JSON.

Для справки: JSON это сокращение от JavaScript Object Notation – формата передачи данных. Как можно понять из названия, JSON произошел из


Рисунок 6.1 — Управление микроконтроллерами с помощью Raspberry Pi

JavaScript, но он доступен для использования на многих других языках, включая Python, Ruby, PHP и Java, в англоязычным странах его в основном произносят как Jason, то есть как имя ДжЭйсон. Легкочитаемый и компактный, JSON представляет собой хорошую альтернативу XML и требует куда меньше форматирования контента.

Объект JSON это набор данных в формате ключ-значение, который находится в фигурных скобках. Вот так выглядит JSON объект:

{
"first_name" : "Anton",

"last_name" : "Kolomeytsev", "location" : "Moscow",

"online" : true,

"languages" : ["Russian", "English"]

}

Массив байт, отправляемый на микроконтроллер, всегда имеет одну и ту же структуру, которую легко расшифровать. Каждая команда имеет свой идентификатор (число от 0 до 255), а также может не иметь вовсе, либо иметь ограниченное числом 256⁴ количество аргументов.

При отправке инструкции на микроконтроллер первым байтом всегда идет номер (идентификатор) команды. Вторым байтом идет число – количество аргументов. Если у команды нет аргументов, байт нулевой. Пример команды без аргументов с идентификатором 207:

идентификатор команды
⏞ | ⏟
11001111 | 00000000
⏟ | ⏞
количество аргументов

К каждому идентификатору можно привязать выполнение роботом какоголибо действия. Например, включение или выключение компрессора, и т.д. Но бывает, что нужно уточнить параметры выполнения команды какими-то числовыми аргументами. В таком случае второй байт будет ненулевым и он будет указывать на количество идущих после второго байта блоков длиной в 4 байта. В каждом таком четырёхбайтном блоке хранится вещественное число. Пример команды с идентификатором 209 с одним вещественным аргументом:

идентификатор команды
⏞ | ⏟
11010001 | 00000001
⏟ | ⏞
количество аргументов

вещественный аргумент
⏞ | ⏟
10110001 11100010 00110100 00100100

Таким образом можно реализовать команду, которой передаются, например, требуемые скорости вращения колес, или параметры чувствительности датчиков, и т.д.

Преимущества выбранного подхода:

- Микроконтроллер способен очень быстро расшифровать массив байт. Поэтому задержка между отправкой команды и её исполнением для человека не заметна.
- Невозможно перенести высокоуровневый функционал и принятие решений на микроконтроллер. Это заставляет продумывать структуру системы.
- При таком формате общения между устройствами разработка укладывается в основы теории автоматического управления.
- Возможность подключить до четырёх микроконтроллеров к одному Raspberry Pi.

Протокол

Правила, по которым устанавливается соединение, следующие:

1. Raspberry Pi устанавливает соединение с Arduino по USB, открывая Serial порт между устройствами.
2. Arduino отправляет свой уникальный идентификатор.
3. После получения идентификатора Raspberry может использовать его для обмена данными.

При написании кода на Raspberry, есть всего три простых функции:

Функция push: отправляет команду под номером CODE с аргументами ARG

clapi.device_id.push(CODE[, ARG1, ARG2, ..., ARGN])

Функция pull: блокирует выполнение программы, дожидается входящего сообщения от устройства. Возвращает JSON, который нам прислало устройство.

clapi.device_id.pull()

Функция request: отправляет команду как push, после чего дожидается ответа как pull.

clapi.device_id.request(CODE[, ARG1, ARG2, ..., ARGN])

Первая версия кода библиотеки для управления была написана в 2019 году, использовалась «в боевых условиях» и достойно показала себя на робототехнических соревнованиях Eurobot. С тех пор код был доработан, дополнительно протестирован и оптимизирован под новые нужды.

### 6.3 Кинематические расчеты

Перенос расчётов из систем математических расчетов вроде Matlab, SciLab или Mathematica на один из языков программирования это не всегда тривиальная задача. Самая сложная часть переноса – матричные вычисления, элементы математического анализа (пределы, производные, интегрирование), решение систем СЛАУ, решение систем нелинейных уравнений. При переносе кинематических расчётов в рамках данного проекта понадобилось реализовать численно следующие функции:

- Вычисление графа прямой кинематики
- Решение тригонометрической задачи о четырехзвеннике

- Вычисление Якобиана
- Решение обратной задачи кинематики

Использование библиотеки численной математики Nupmy на языке программирования Python сильно упростило задачу. Стоит отметить что Numpy сегодня активно используется для математических вычислений исследователями всех стран.
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

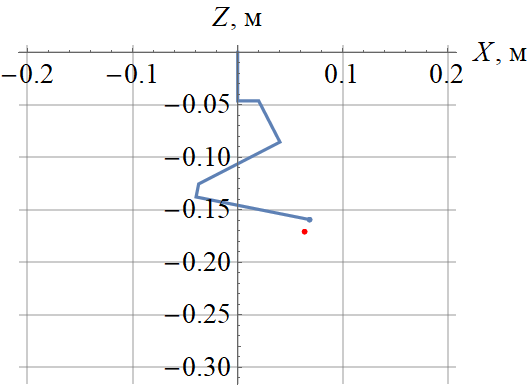
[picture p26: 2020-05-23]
diploma/chapter_kinematics/figure6.png

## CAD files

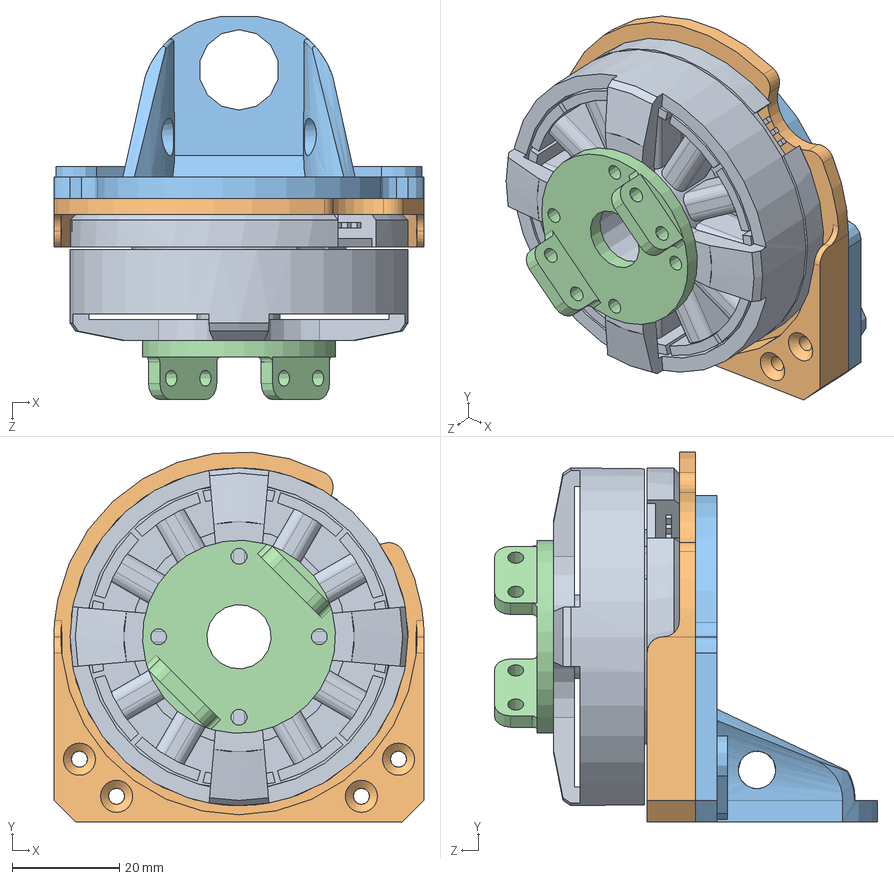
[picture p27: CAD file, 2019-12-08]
стенд_bldc/Сборка стенда для BLDC.SLDASM
69.0 x 68.9 x 71.5 mm
BGM5208-200-12
Часть корпуса 1
Часть корпуса 2
Крепеж линейки

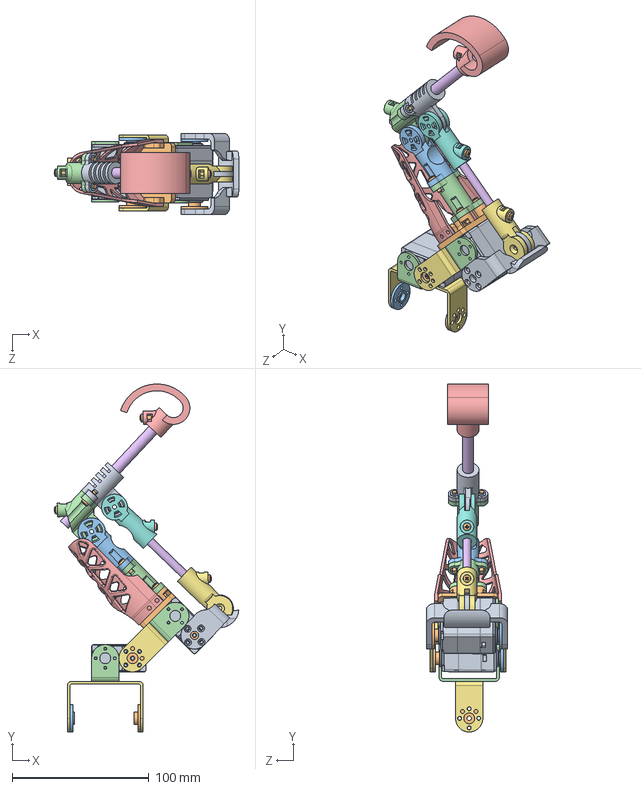
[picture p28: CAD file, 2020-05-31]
робот/Сборка Ноги.SLDASM
135.2 x 254.8 x 59.6 mm
SERVO rds3115-3d v3 x 2
Втулка серво 1 x 3
Втулка серво 2 x 3
КРОНШТЕЙН_ЗАДНИЙv2 x 2
Звено 2 - Стержень несущий
Стержень Аллюминиевый
КРОНШТЕЙН_1v2 x 2
Подшипник 3mm (3x10x4) x 3
Кронштейн_Сухожилие
Крепеж ведущего стержня
Колено-Узел
Колено-Узел2
Стопа
четырехзвенник1
Колено-Узел3
Колено-Узел4
Колено-Узел5
pan head cross recess screw_iso x 11
hex thin nut gradeb_iso x 2
Ответочка на крепеж ведущего стержня
Декор корпус

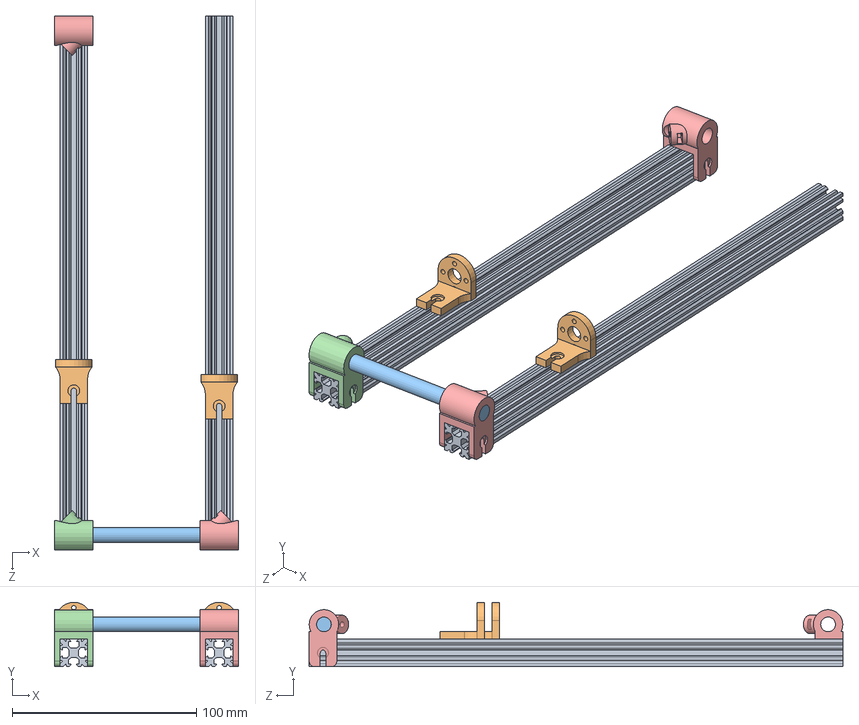
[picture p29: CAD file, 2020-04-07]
робот/Сборка тела.SLDASM
100.0 x 35.0 x 290.0 mm
Профиль 15х15 x 2
Крепеж ноги к корпусу КРУГЛЫЙ x 2
Передний верхний профиль тела
Крепеж перхней фермы тела
[Mirrored] Крепеж перхней фермы тела x 2

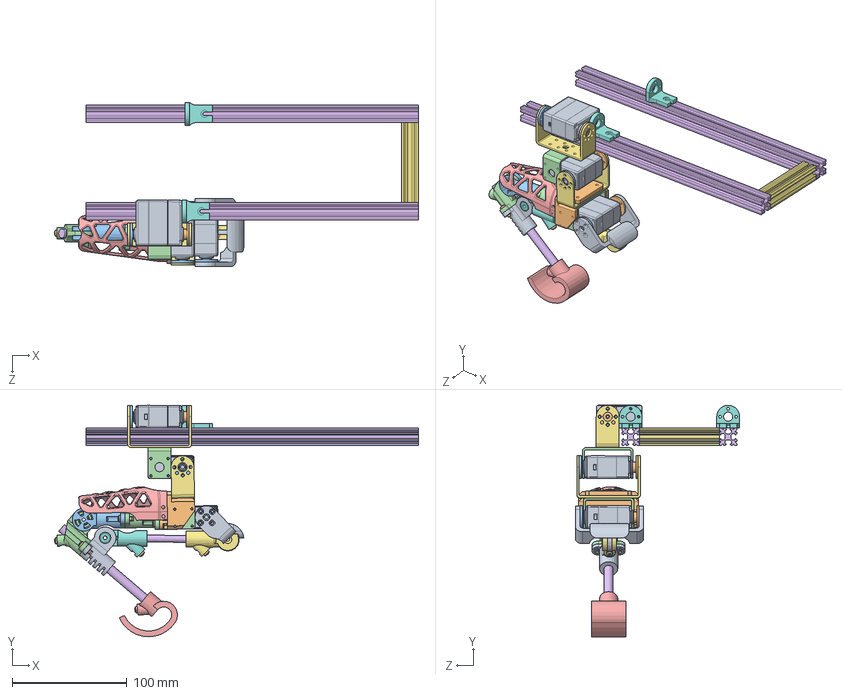
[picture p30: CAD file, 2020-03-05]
робот/Сборка робота.SLDASM
317.4 x 201.9 x 143.2 mm
SERVO rds3115-3d v3 x 3
Втулка серво 1 x 3
Втулка серво 2 x 3
КРОНШТЕЙН_ЗАДНИЙv2 x 2
Звено 2 - Стержень несущий
Стержень Аллюминиевый
КРОНШТЕЙН_1v2 x 2
Подшипник 3mm (3x10x4) x 3
Кронштейн_Сухожилие
Крепеж ведущего стержня
Колено-Узел
Колено-Узел2
Стопа
четырехзвенник1
Колено-Узел3
Колено-Узел4
Колено-Узел5
pan head cross recess screw_iso x 11
hex thin nut gradeb_iso x 2
Ответочка на крепеж ведущего стержня
Декор корпус
Профиль 15х15 x 2
Профиль 15х15 (2)
Крепеж ноги к корпусу КРУГЛЫЙ x 2

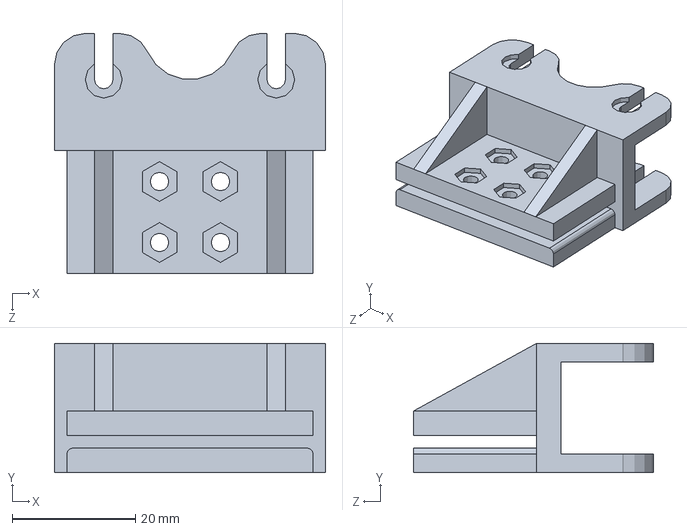
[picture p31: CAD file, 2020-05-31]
робот/Крепеж ноги к корпусу КРУГЛЫЙ.SLDPRT
44.0 x 21.0 x 39.0 mm

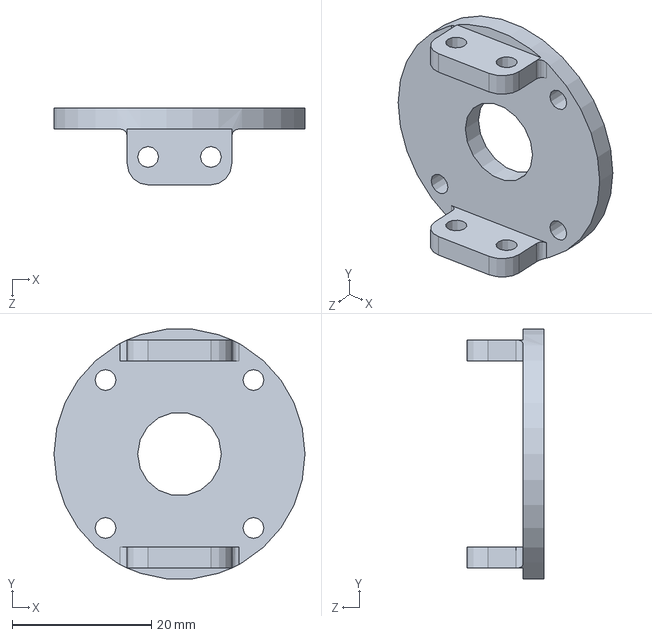
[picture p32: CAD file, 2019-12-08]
стенд_bldc/Крепеж линейки.SLDPRT
36.0 x 35.8 x 11.0 mm

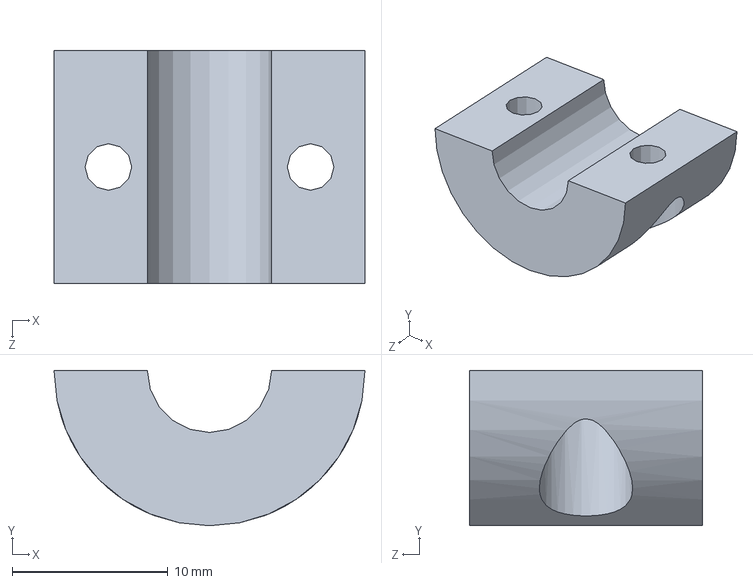
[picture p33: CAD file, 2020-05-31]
робот/Разъемное крепление короба.SLDPRT
20.0 x 10.0 x 15.0 mm

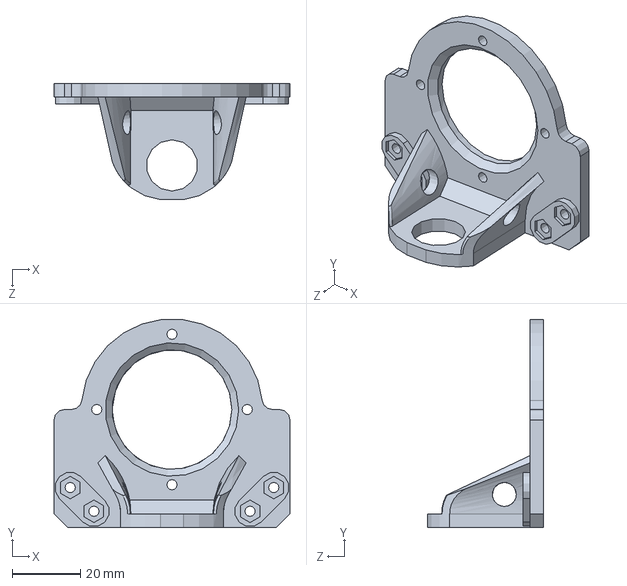
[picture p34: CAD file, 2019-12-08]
стенд_bldc/Часть корпуса 2.SLDPRT
69.0 x 60.8 x 34.0 mm

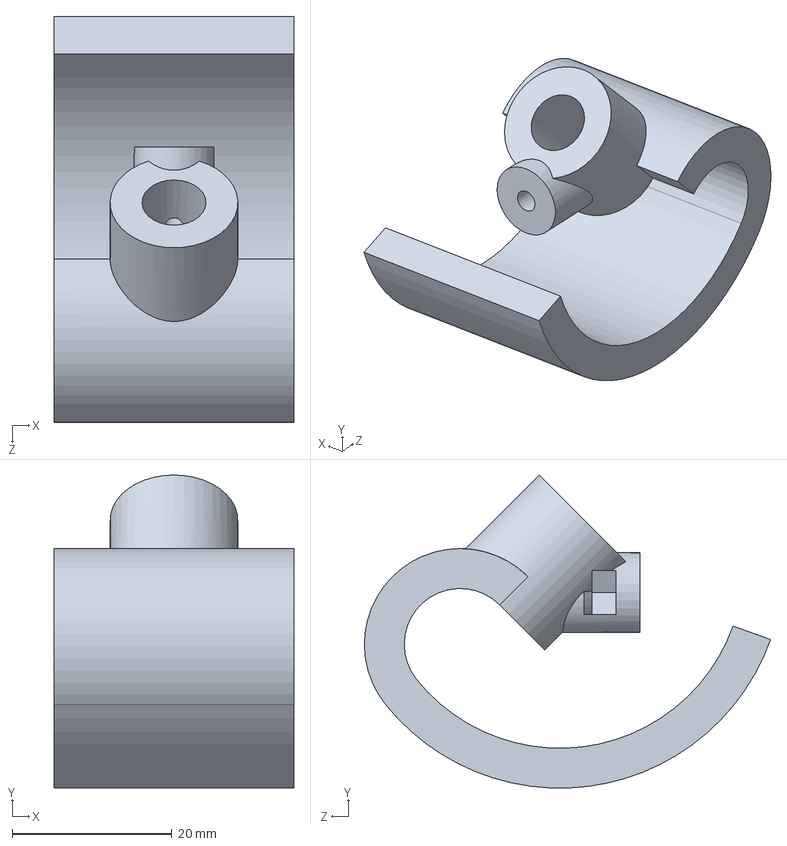
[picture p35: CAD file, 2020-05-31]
робот/Стопа.SLDPRT
30.0 x 39.2 x 50.9 mm

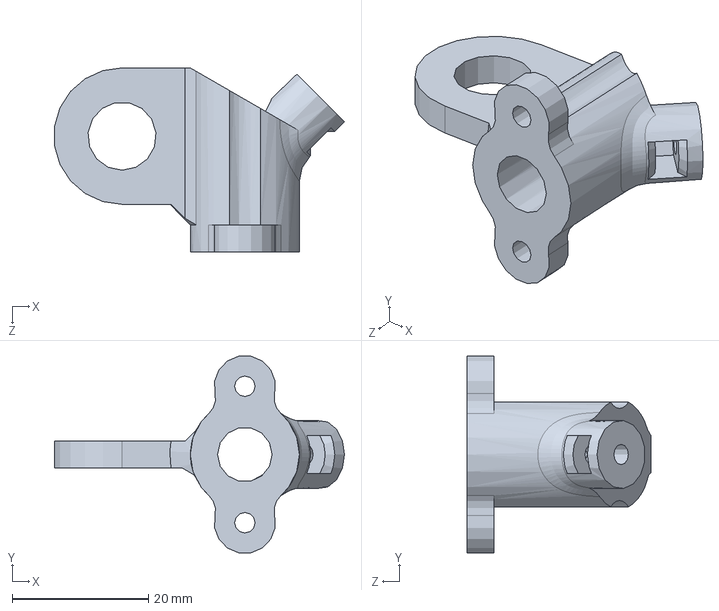
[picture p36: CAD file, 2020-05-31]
робот/Колено-Узел2.SLDPRT
42.5 x 28.8 x 27.0 mm

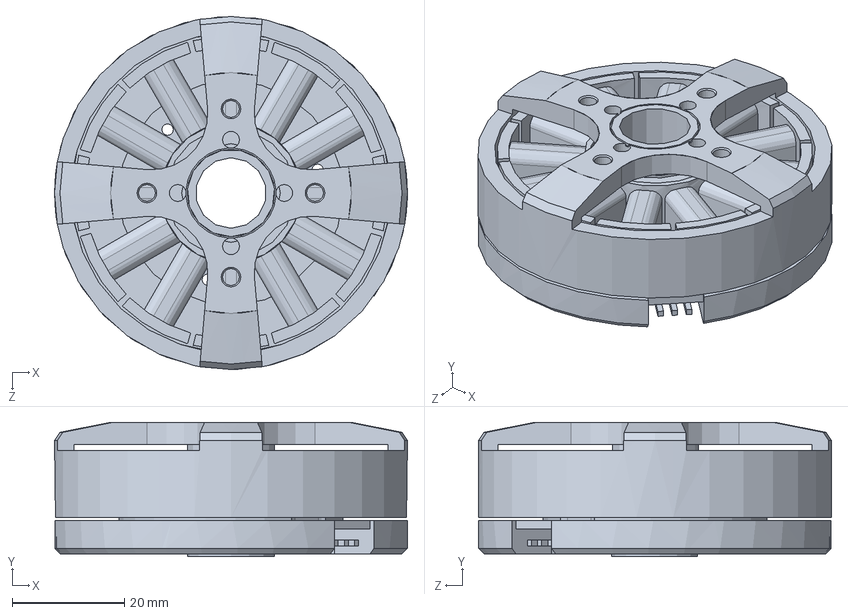
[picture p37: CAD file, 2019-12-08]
стенд_bldc/BGM5208-200-12.SLDPRT
63.0 x 24.0 x 63.0 mm

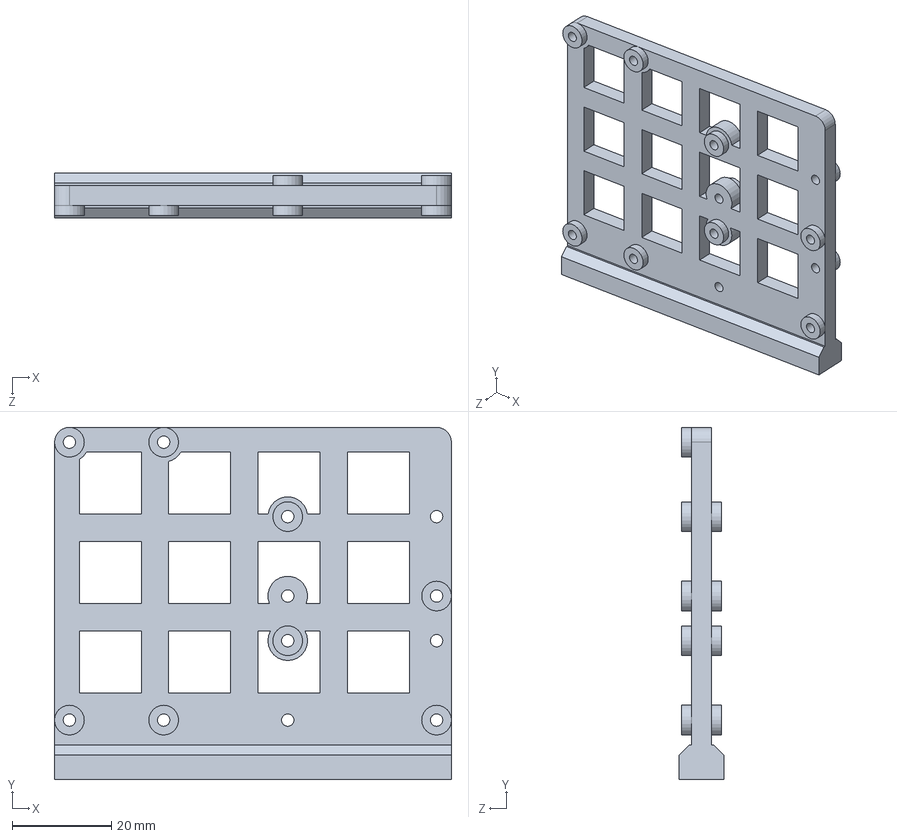
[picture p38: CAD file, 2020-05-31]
робот/Крепеж драйвера и преобразователей.SLDPRT
80.0 x 71.0 x 9.00 mm

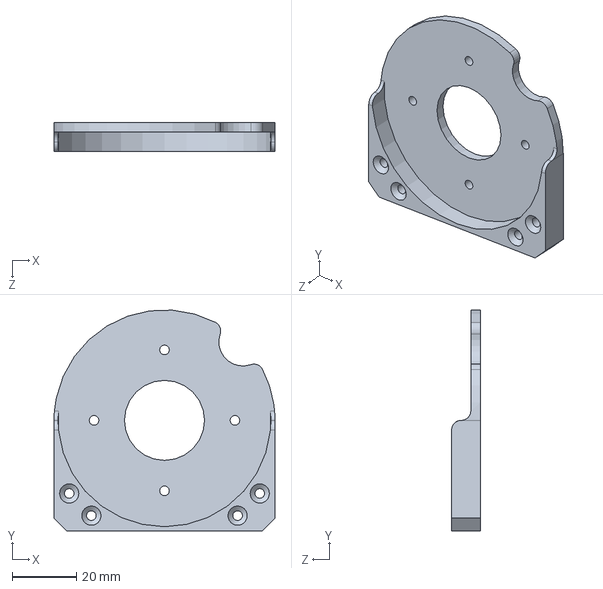
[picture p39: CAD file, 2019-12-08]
стенд_bldc/Часть корпуса 1.SLDPRT
69.0 x 68.9 x 9.00 mm

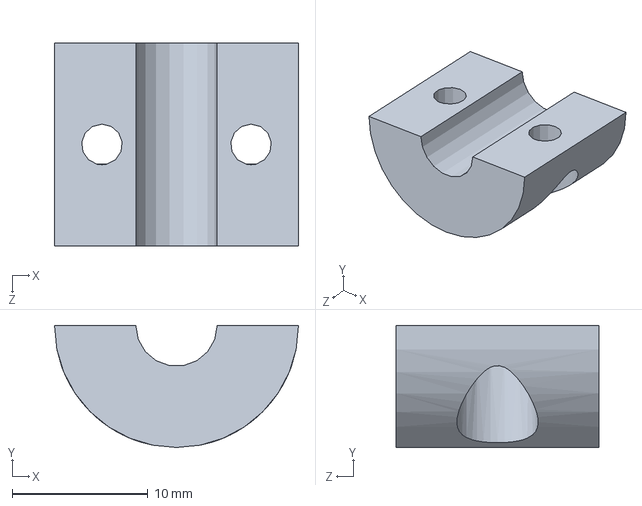
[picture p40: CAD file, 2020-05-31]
робот/Разъемное крепление короба (6 мм).SLDPRT
18.0 x 9.00 x 15.0 mm

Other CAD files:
робот/Кронштейн_Сухожилие.SLDPRT
робот/Ответочка на крепеж ведущего стержня.SLDPRT
робот/Держатель аккумулятора.SLDPRT
робот/Крепеж логических компонентов.SLDPRT
робот/Adafruit PWM Servo Driver with PCA9685.SLDPRT
робот/Arduino.SLDPRT
робот/LM2596 DC-DC StepDown Converter v1.SLDPRT
робот/SERVO rds3115-3d v3.SLDPRT
робот/TOWER PRO MG-995, ANALOG SERVO v2.SLDPRT
робот/[Mirrored] Крепеж перхней фермы тела.SLDPRT
робот/makeProjectedPlanarWire.x_t
робот/Аккумулятор.SLDPRT
робот/Втулка серво 1.SLDPRT
робот/Втулка серво 2.SLDPRT
робот/Декор корпус.SLDPRT
робот/Звено 2 - Стержень несущий.SLDPRT
робот/КРОНШТЕЙН_1.SLDPRT
робот/КРОНШТЕЙН_1v2.SLDPRT
робот/КРОНШТЕЙН_ЗАДНИЙ.SLDPRT
робот/КРОНШТЕЙН_ЗАДНИЙv2.SLDPRT
робот/Колено-Узел.SLDPRT
робот/Колено-Узел3.SLDPRT
робот/Колено-Узел4.SLDPRT
робот/Колено-Узел5.SLDPRT
робот/Крепеж ведущего стержня.SLDPRT
робот/Крепеж перхней фермы тела.SLDPRT
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

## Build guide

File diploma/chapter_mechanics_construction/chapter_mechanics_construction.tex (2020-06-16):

\chapter{\MakeUppercase{Механическая конструкция}}
\section{Проектирование ног} \label{sec:leg_design}
Основная, и самая сложная с точки зрения механики часть шагающего робота это конечности. Как и корпус, ноги проектировались в виде трёхмерных, твердотельных чертежей. Для уменьшения количества уникальных деталей конструкция всех четырех ног была унифицирована (рисунки \ref{fig:the_same_legs} и \ref{fig:the_same_details}). Таким образом снижена сложность и затратность в производстве деталей. 

\begin{figure}[h]
    \centering
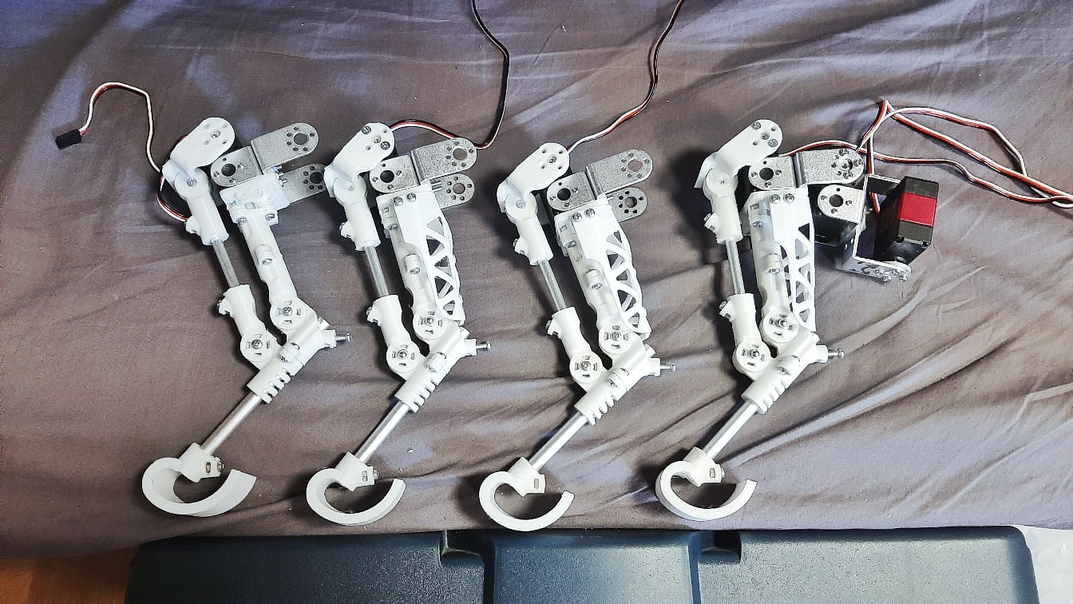
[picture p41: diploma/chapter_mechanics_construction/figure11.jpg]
    
    \caption{Конструкции всех четырех ног унифицированы}
    \label{fig:the_same_legs}
\end{figure}

Сложные по форме детали изготовлены из пластика на 3D-принтере, в конструкции также присутствуют металлические стержни, стандартные металлические кронштейны, крепежные элементы (винты, гайки).

Перед проектированием были выдвинуты функциональные требования к конечностям. Они должны быть как можно менее габаритными, для сохранности редукторов сервоприводов и для увеличения скорости движения нужно максимально уменьшить момент инерции конечности. Основной способ достижения этой цели -- уменьшение веса всех деталей. Поэтому некоторые крепежи и элементы корпуса, по возможности, были изготовлены из пластика. Были использованы полые цилиндрические алюминиевые трубки в качестве стержней, обеспечивающих жесткость.

\begin{figure}[h]
    \centering
    
    \caption{Сервоприводы \textit{DSSERVO RDS3225}, использованные в прототипе робота}
    \label{fig:servo_demo}
\end{figure}

Есть еще один, не менее эффективный способ снизить момент инерции ног, не уменьшая общего веса конечностей -- концентрация основной массы как можно выше \cite{Seok2012}, ближе к месту крепления ноги к корпусу. Поэтому сервоприводы (рис.~\ref{fig:servo_demo}), как одни из самых тяжелых элементов конструкции, были перенесены как можно ближе к корпусу и как можно дальше от пола. Получившаяся конструкция изображена на рисунках \ref{fig:figg7} и \ref{fig:two_states}.

\begin{figure}[h]
    \centering
    
    \caption{Твердотельный чертеж конечности робота. Можно заметить что двигатели размещены у основания конечности.}
    \label{fig:figg7}
\end{figure}

Двигатель неудобно размещать в узле в силу конструктивных особенностей. В связи с этим в конструкции возник механический четырехзвенник, позволяющий передавать вращение стержневых элементов. Четырехзвенник усложнил кинематическую схему ноги, его расчет рассмотрен далее в пункте \ref{sec:pre_direct_kin}, однако такая конструкция позволила уменьшить габариты конечности и положительно повлияла на её эстетические качества. 

\begin{figure}[h]
    \centering
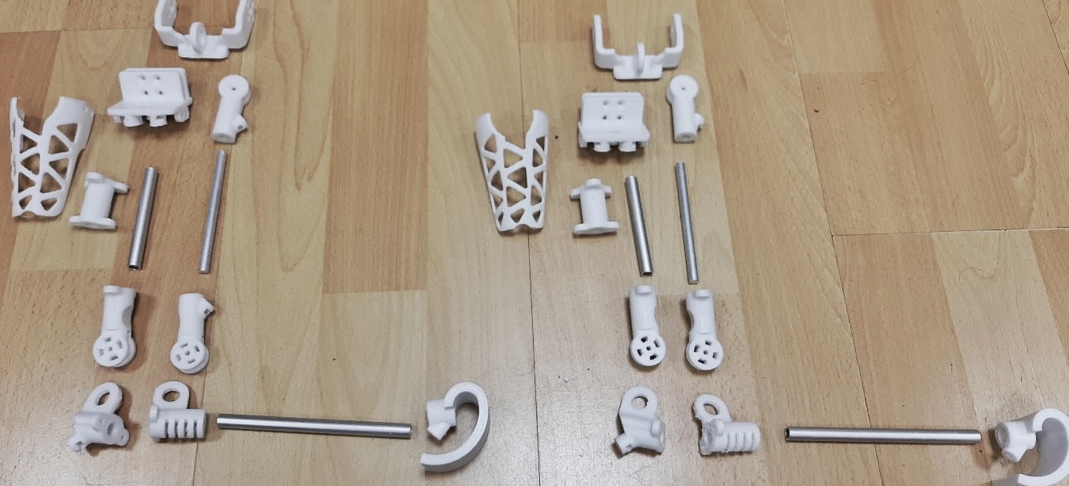
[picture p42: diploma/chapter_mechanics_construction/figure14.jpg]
    
    \caption{Набор унифицированных деталей для изготовления конечностей.}
    \label{fig:the_same_details}
\end{figure}

\begin{figure}[h]
    \centering
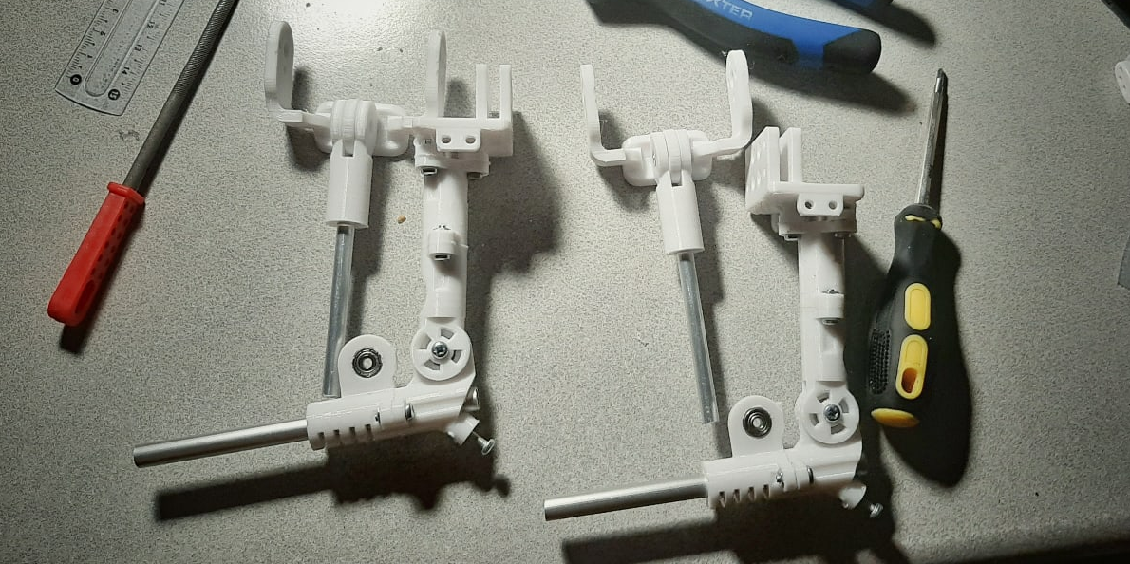
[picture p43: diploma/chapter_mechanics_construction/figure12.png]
    
    \caption{Процесс сборки конечностей. Используются полые алюминиевые стержни и пластиковые детали.}
    \label{}
\end{figure}

% ввести термины "стопы" и другие в описании кинематики
\newpage
В конструкции предусмотрена установка датчиков касания на стопы. Конструкция ноги позволит без проблем проложить провода так, чтобы их не было видно.
\begin{figure}[ht]
    \centering
    % левая картинка
    \begin{subfigure}[b]{0.45\textwidth}    
        \centering
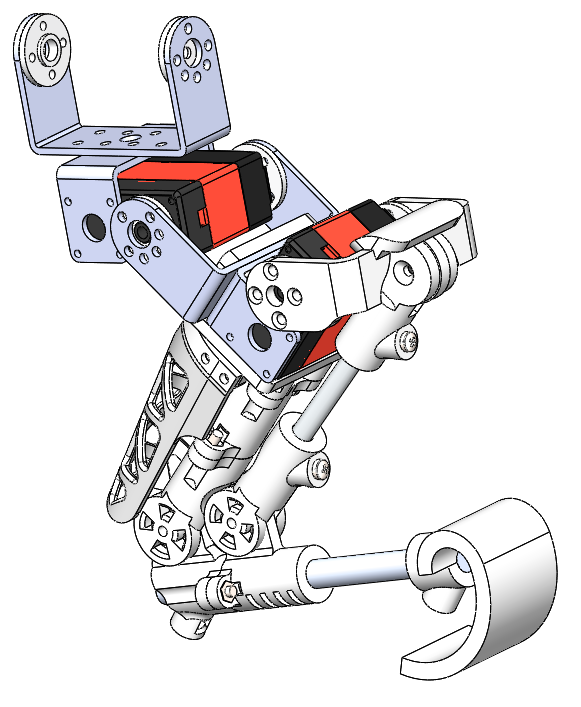
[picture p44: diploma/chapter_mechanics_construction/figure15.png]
        
        \caption{Последнее звено согнуто}
    \end{subfigure}
    % правая картинка  
    \begin{subfigure}[b]{0.45\textwidth}
        \centering
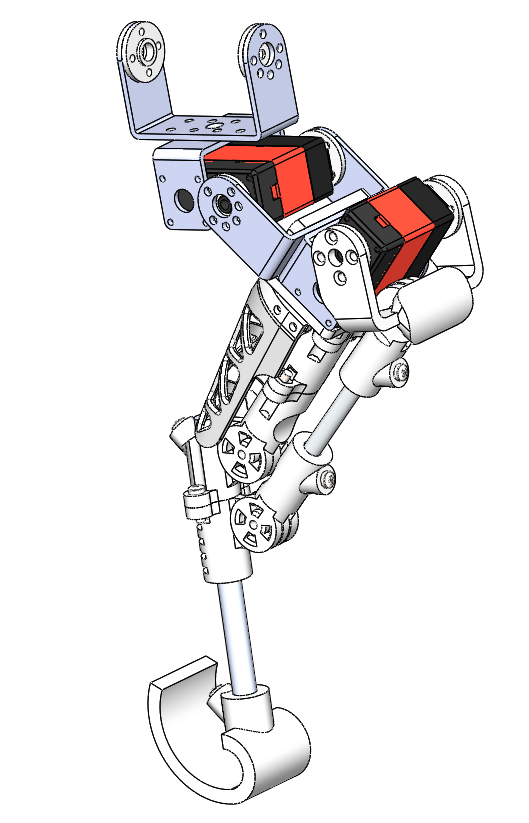
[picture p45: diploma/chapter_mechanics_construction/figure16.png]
        
        \caption{Последнее звено разогнуто}
    \end{subfigure}
     
    \caption{Конечность в двух состояниях}
    \label{fig:two_states}
\end{figure}

Из-за специфики сервоприводов возникают проблемы, которые замедляют процесс сборки и требуют наличия управляющей электроники. В используемых сервоприводах установлены абсолютные датчики угла поворота вала (энкодеры). Такой сервопривод при установке в конструкцию должен быть верно сконфигурирован, или проще говоря, нужно, чтобы вал сервопривода был заранее повернут на известный управляющей программе угол (<<технический>> угол). Эту особенность можно считать минусом, так как в приводах с относительными энкодерами конфигурировать углы поворота при сборке не нужно. Однако во время использования таких приводов нужно проводить калибровку, поворачивая их в нулевое, начальное положение. Перевод в начальное положение подразумевает наличие концевых выключателей в конструкции. Такие приводы не были использованы в силу своей дороговизны и в силу того, что наличие концевых выключателей сильно бы усложнило разработку. Для прототипа это излишне.

\section{Проектирование корпуса}
Требования к корпусу можно разделить на три составляющие: массовые, габаритные и эстетические. Снижать массу нужно для того чтобы разгрузить конечности робота, защитить редукторы электроприводов. Снижению массы способствует максимальный отказ от металлических деталей, а там где это невозможно (в силу требований по жесткости), нужно использовать эффективные сечения профилей, желательно из алюминия.

В качестве каркаса, к которому крепятся ноги робота, был выбран конструкционный алюминиевый профиль (рис.~\ref{fig:profile1}), из-за его легкости, жесткости и простоты крепления новых деталей к профилю.
\begin{figure}[ht]
    \centering
    % левая картинка
    \begin{subfigure}[b]{0.45\textwidth}    
        \centering
        
        \caption{Сечение профиля}
    \end{subfigure}
    % правая картинка  
    \begin{subfigure}[b]{0.45\textwidth}
        \centering
        
        \caption{Внешний вид профиля}
    \end{subfigure}
     
    \caption{Конструкционный алюминиевый профиль}
    \label{fig:profile1}
\end{figure}

Объем корпусу придают тонкие цилиндрические алюминиевые стержни и пластиковые детали в качестве передней и задней стенок (рисунок~\ref{fig:korpus1}). В узлах между металлическими профилями используются пластиковые крепежи. Такая конструкция позволяет использовать много свободного места внутри корпуса, что упрощает размещение электронных компонентов внутри.

\begin{figure}[h]
    \centering
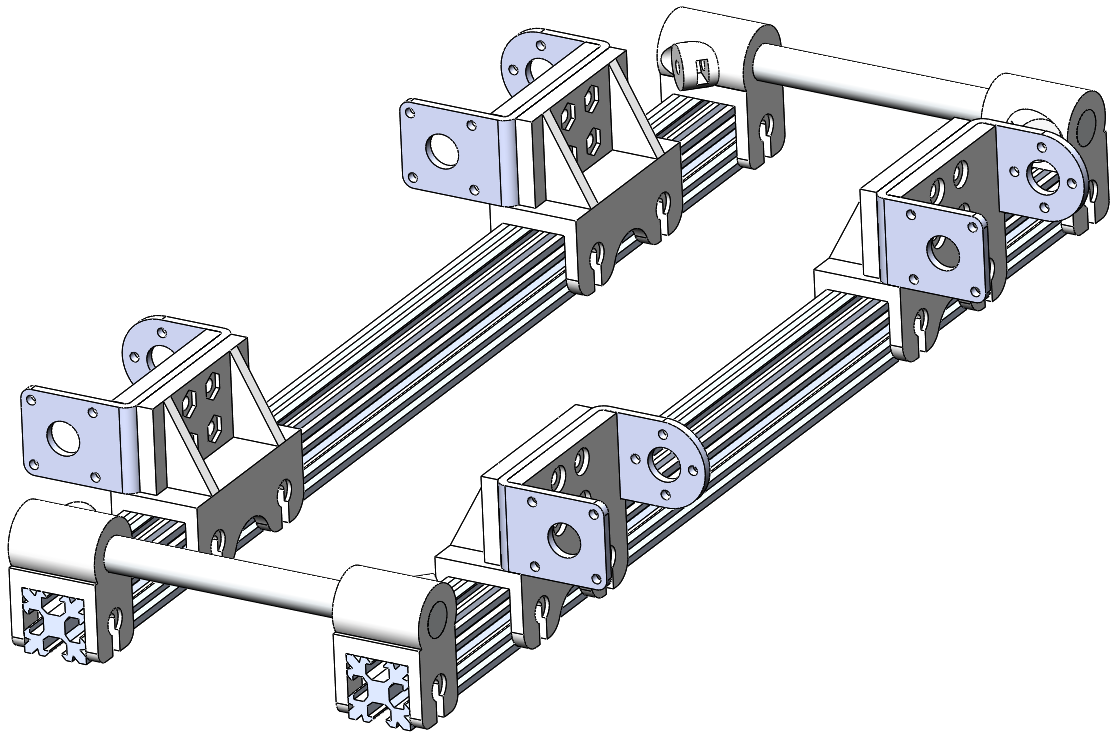
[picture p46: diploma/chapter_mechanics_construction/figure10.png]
    
    \caption{Основной каркас корпуса}
    \label{fig:karkas1}
\end{figure}

\newpage
Самой сложной задачей было размещение всех компонентов внутри корпуса, так как нужно обеспечить удобный доступ к ним в любой момент времени для замены или диагностики. Таким образом, повышается общая ремонтопригодность прототипа, а это сильно ускоряет работу с ним.

\begin{figure}[h]
    \centering
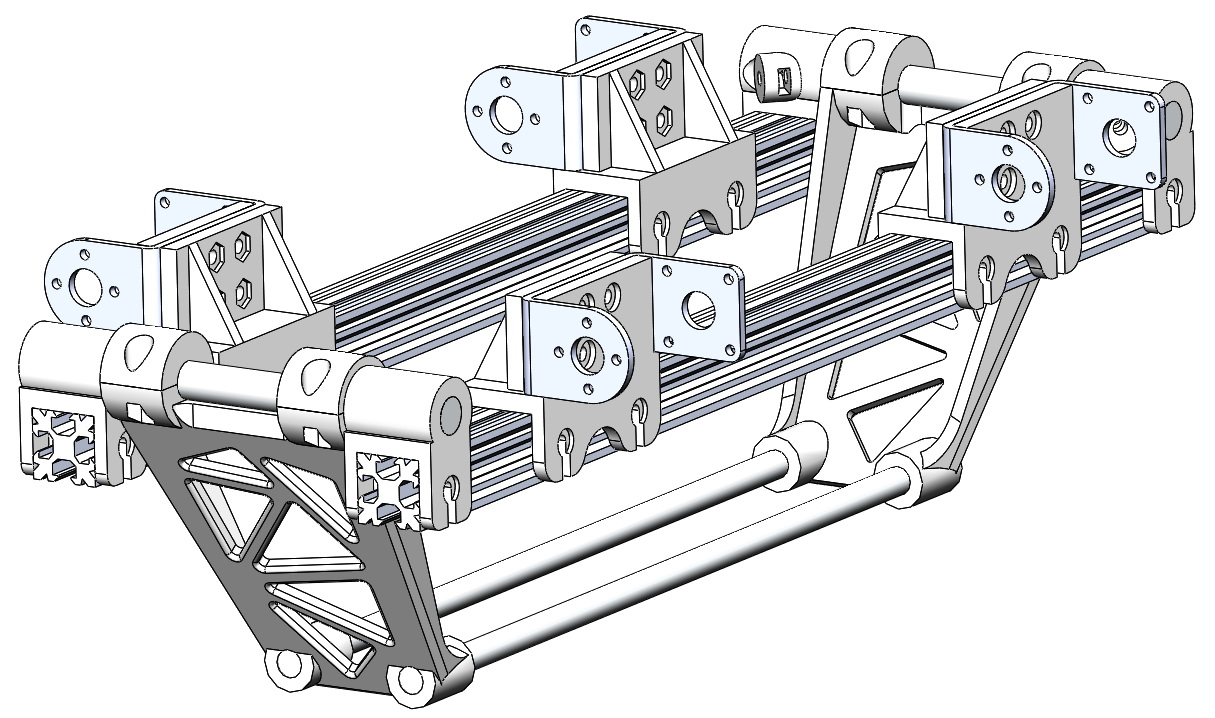
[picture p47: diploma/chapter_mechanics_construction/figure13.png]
    
    \caption{Короб, скрепленный с корпусом}
    \label{fig:korpus1}
\end{figure}

Чтобы максимально облегчить работу над монтажем электроники, был разработан электронный блок, целиком вынимающийся из корпусного короба (рисунок~\ref{fig:electro_blok}). У такого решения есть как преимущества, так и недостатки. Важно, что в таком состоянии сохраняется <<наглядность>> электронной схемы, легкий доступ воздуха к компонентам, исключающий факт перегрева и последующего выхода из строя по причине того что перегрев не был вовремя замечен.
\begin{figure}[ht]
    \centering
    % левая картинка
    \begin{subfigure}[b]{0.45\textwidth}    
        \centering
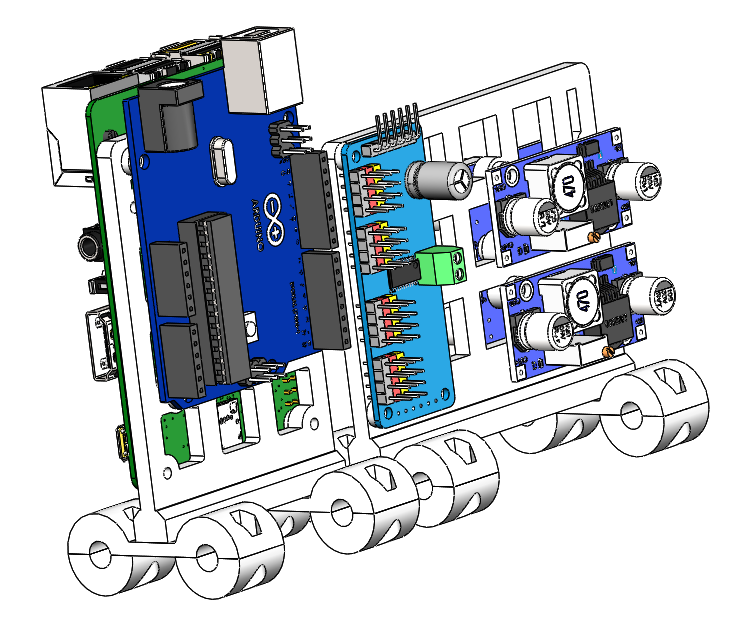
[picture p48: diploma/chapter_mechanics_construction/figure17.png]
        
        \caption{}
    \end{subfigure}
    % правая картинка  
    \begin{subfigure}[b]{0.45\textwidth}
        \centering
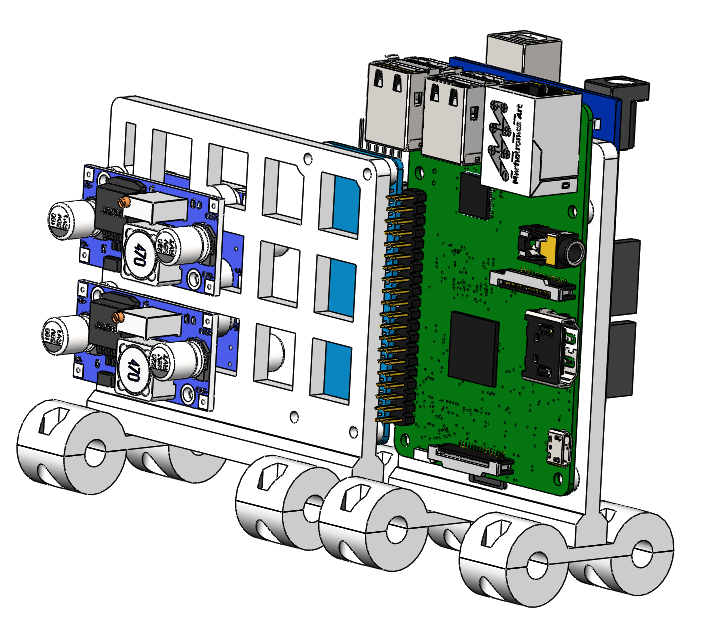
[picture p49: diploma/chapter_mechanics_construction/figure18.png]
        
        \caption{}
    \end{subfigure}
     
    \caption{Электронный блок с разных сторон}
    \label{fig:electro_blok}
\end{figure}

Такой электронный блок монтируется на стержни нижней части корпуса, что позволяет менять его положение и порядок установки даже после сборки робота. Корпус робота с электронным блоком и аккумулятором представлен на рисунке \ref{fig:full_body}.
\begin{figure}[h]
    \centering
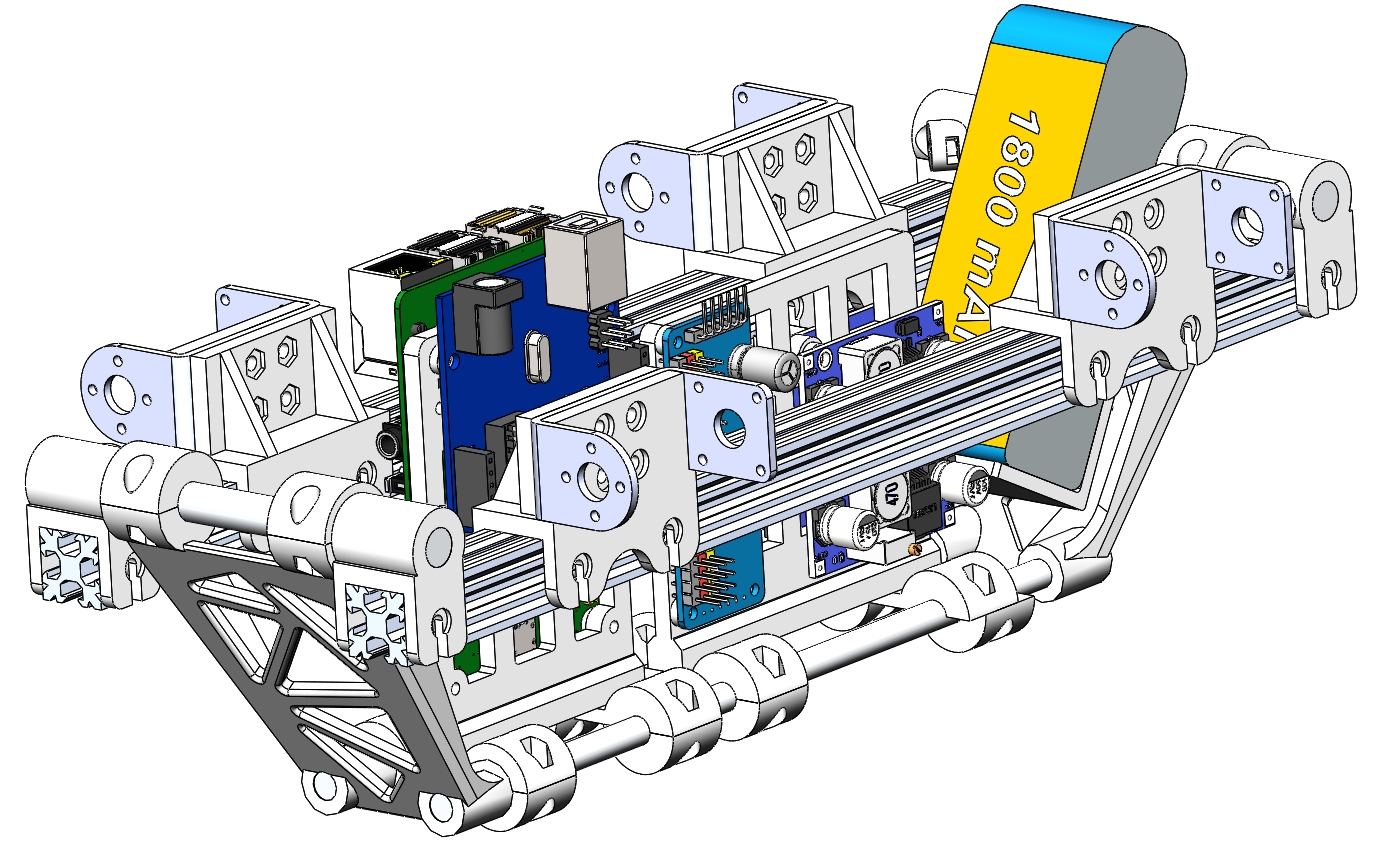
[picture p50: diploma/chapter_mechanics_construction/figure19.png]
    
    \caption{Корпус робота с электронным блоком и аккумулятором}
    \label{fig:full_body}
\end{figure}

\section{Подбор комплектующих}
\subsection{Силовая электроника}
Из силовой электроники в роботе присутствуют:
\begin{itemize}
    \item сервоприводы;
    \item преобразователи постоянного напряжения.
\end{itemize}

Исходя из ожидаемых моментов и скоростей, был выбран заводской сервопривод \textit{DSSERVO RDS3225}.

Используются одни из самых компактных и простых в настройке преобразователей напряжения. В основном используются импульсные преобразователи напряжения на базе микросхем \textit{LM-XXXX} и \textit{XL-XXXX} (рисунок~\ref{fig:dcdc_converters}). Они хорошо взаимозаменяемы друг с другом. Для двух пар ног выбраны два преобразователя с максимальным током нагрузки $ 5 \: А $. Для питания логической части используется преобразователь с током нагрузки $ 3 \: А $.
\begin{figure}[ht]
    \centering
    % левая картинка
    \begin{subfigure}[b]{0.45\textwidth}    
        \centering
        
        \caption{Преобразователь на базе \textit{LM2596S}}
    \end{subfigure}
    % правая картинка  
    \begin{subfigure}[b]{0.45\textwidth}
        \centering
        
        \caption{Преобразователь на базе \textit{LM2577}}
    \end{subfigure}
     
    \caption{Силовая электроника в составе робота}
    \label{fig:dcdc_converters}
\end{figure}

\subsection{Логическая электроника}
В качестве управляющего микрокомпьютера выступает \textit{Raspberry Pi 3B+}. Этого достаточно для совершения множества матричных операций в секунду и для эффективной работы с высокоуровневыми абстракциями в коде.

\begin{figure}[ht]
    \centering
    % левая картинка
    \begin{subfigure}[b]{0.45\textwidth}    
        \centering
        
        \caption{\textit{Arduino Uno}}
    \end{subfigure}
    % правая картинка  
    \begin{subfigure}[b]{0.45\textwidth}
        \centering
        
        \caption{\textit{Raspberry Pi 3B+}}
    \end{subfigure}
     
    \caption{Логическая электроника в составе робота}
    \label{fig:leg_model}
\end{figure}

\textit{Raspberry Pi} выступает исключительно как своеобразный модуль для высокоуровневых вычислений и не работает с <<железом>> напрямую. Вместо этого происходит отправка команд на микроконтроллер в составе платформы \textit{Arduino}. Команды формируются и передаются в цифровом виде на микроконтроллер. Сделано это по двум причинам:
\begin{itemize}
    \item Разграничение логики вычислений состояния робота от процесса управления (подробнее в главе \ref{chap:arch}). % в главе 6 подробнее описано
    \item Электрическая защита дорогостоящего микрокомпьютера от возможных скачков тока в цепи силовой электроники.
\end{itemize}

О протоколе передачи данных и способе формирования команд подробнее написано в пункте \ref{sec:protocol}.

\section{Аккумулятор}
В качестве аккумулятора был использован Литий-полимерный аккумулятор (\textit{Li-Po} аккумулятор). Преимущества аккумуляторов таких типов:
\begin{itemize}
    \item высокая токоотдача;
    \item большая емкость;
    \item быстрая зарядка;
    \item наличие дешевой электроники для контроля разряда таких аккумуляторов;
    \item малый вес и габариты;
\end{itemize}

\begin{figure}[h]
    \centering
    
    \caption{\textit{Li-Po} аккумулятор на 2600 мА$\cdot$ч}
    \label{}
\end{figure}

С такими большими плюсами существуют и минусы, которые стоит принимать во внимание при эксплуатации такого типа аккумуляторов:
\begin{itemize}
    \item Высокая токоотдача повышает риск получить травму при работе
    \item Высоки шансы на сгорание питающейся от аккумулятора электроники в случае короткого замыкания
    \item Требуются специальные условия хранения, если аккумуляторы долгое время не используются
    \item \textit{Li-Po} аккумуляторы взрывоопасны при неправильной эксплуатации
\end{itemize}

\section{Остальные детали}
Пластиковые детали изготавливались на \textit{3D}-принтере методом \textit{FDM} печати (послойной) из материала \textit{PET-G}, характеристики которого близки к материалу \textit{ABS} \cite{Filament2017}, который широко используется в промышленности, при изготовлении деталей. Преимущества материала для данного робота описаны ниже:
\begin{itemize}
    \item высокая прочность; 
    \item термостойкость (выдерживает нагрев до 200 градусов);
    \item не требователен к условиям печати;
    \item низкая термоусадка (почти не меняет размеры при нагревании/остывании);
    \item возможность красить и стерилизовать;
    \item не токсичен.
\end{itemize}
\begin{figure}[ht]
    \centering
    % левая картинка
    \begin{subfigure}[b]{0.45\textwidth}    
        \centering
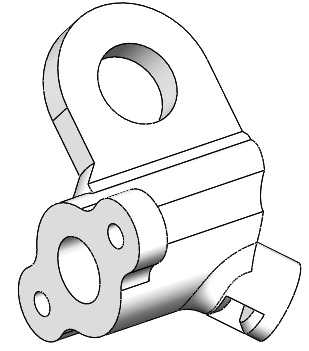
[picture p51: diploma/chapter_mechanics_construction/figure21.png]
        
        \caption{}
    \end{subfigure}
    % правая картинка  
    \begin{subfigure}[b]{0.45\textwidth}
        \centering
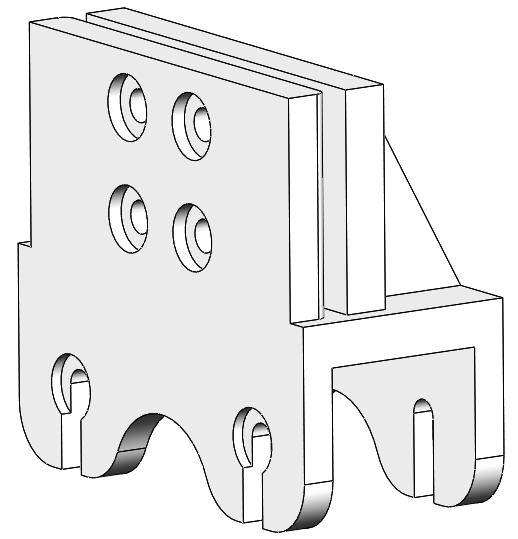
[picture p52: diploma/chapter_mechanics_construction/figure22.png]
        
        \caption{}
    \end{subfigure}
     
    \caption{Примеры деталей, изготовленных на \textit{3D}-принтере}
    \label{}
\end{figure}

Может показаться, что при изготовлении деталей на \textit{3D}-принтере последним можно придавать любую форму, но при \textit{FDM} технологии печати это не так. Технология достаточно дешева и может использоваться в дешевых домашних \textit{3D}-принтерах, поэтому у нее есть свои ограничения на печать <<нависающих>> над печатной областью частей детали (рисунок~\ref{fig:print_demo}). Поэтому при проектировании деталей из пластика нужно исходить из двух принципов. Первый заключается в том чтобы печатать только нестандартные детали, которые невозможно приобрести в розничных магазинах. Второй принцип заключается в том, чтобы использовать в детали как можно меньше материала и скомпоновать ее так, чтобы при печати максимально избежать создания поддержек для нависающих частей. Всё это накладывает свои конструктивные ограничения и требует от конструктора некоторого опыта.

\begin{figure}[h]
    \centering
    
    \caption{Иллюстрация \textit{3D}-печати по технологии \textit{FDM}}
    \label{fig:print_demo}
\end{figure}

Из металла выполнены покупные кронштейны, стержни ног. Стержни -- стандартные полые цилиндрические алюминиевые профили. Подгонялись под нужную длину при помощи ножовки. Крепление к пластиковым узлам происходило вкручиванием в торцы стержней винтов. Такой способ приводит к хорошему сцеплению деталей.

Для того чтобы избежать разрушения пластиковых деталей в месте вкручивания винта в торец, и из-за невозможности нарезать резьбу в пластиковой детали, были использованы вставки из металлических гаек внутри пластикового материала. В целом, из-за гораздо более низкой прочности пластика по сравнению с металлом, в высоконагруженных местах используется большее количество материала, для снижения напряжений.

В ходе тестирования пластиковых деталей на прочность было выявлено, что 100\% заполнение деталей не делает их более устойчивыми к нагрузкам, делает их хрупкими. В то же время детали, с заполнением от 40\% до 60\% не разрушаются. Теряя свои начальные прочностные характеристики, они деформируются, что положительно сказывается на безопасности находящийся рядом узлов конструкции.

\section*{Результат проектирования}

Сборочный чертеж робота представлен на рисунке \ref{fig:final_drawing}. Фотографии собранного прототипа на рисунках \ref{fig:final_assembly1} и \ref{fig:final_assembly2}.

\begin{figure}[h]
    \centering
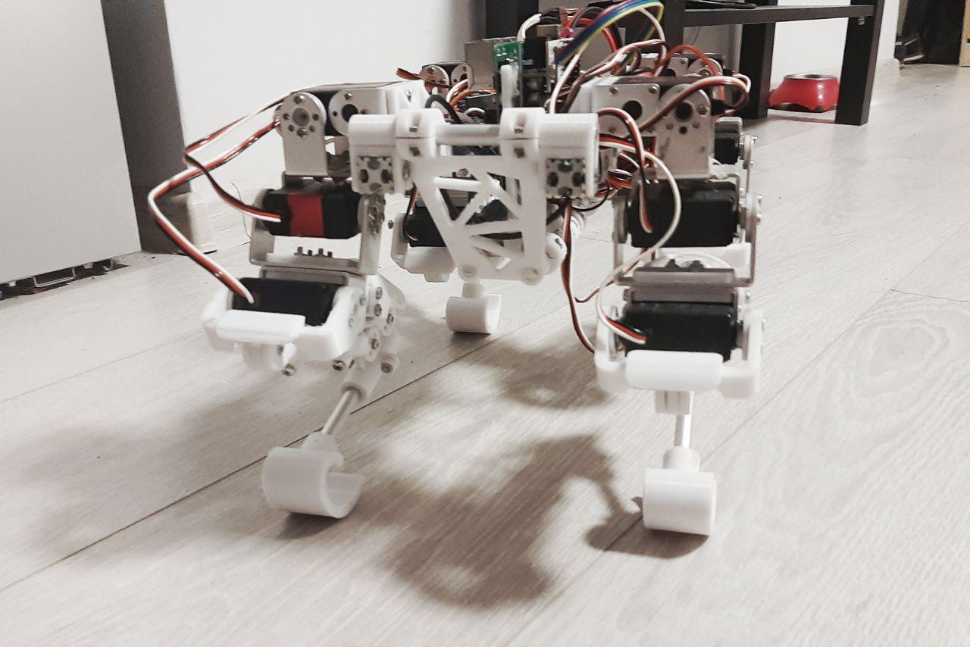
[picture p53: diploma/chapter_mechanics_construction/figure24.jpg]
    
    \caption{Собранный прототип робота, вид спереди}
    \label{fig:final_assembly1}
\end{figure}

\begin{figure}[h]
    \centering
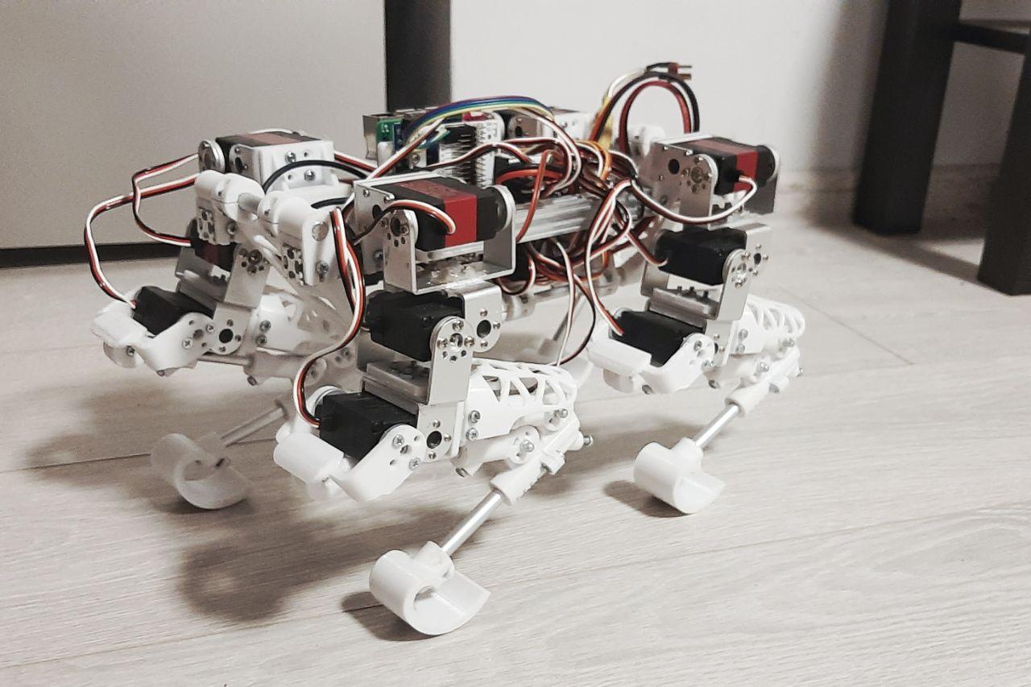
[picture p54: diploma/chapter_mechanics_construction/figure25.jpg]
    
    \caption{Собранный прототип робота, вид сбоку}
    \label{fig:final_assembly2}
\end{figure}

\begin{figure}[h]
    \centering
    
    \caption{Чертеж робота в сборке}
    \label{fig:final_drawing}
\end{figure}

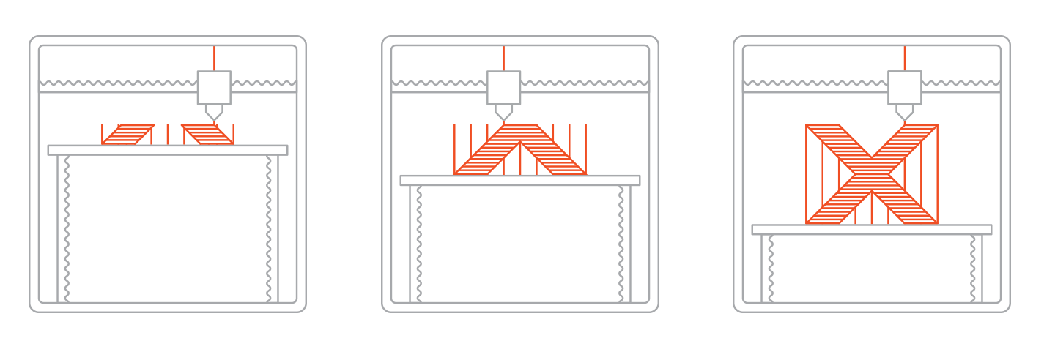
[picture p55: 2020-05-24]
diploma/chapter_mechanics_construction/figure1.png

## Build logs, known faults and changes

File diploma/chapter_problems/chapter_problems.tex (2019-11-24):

\chapter{\MakeUppercase{Конечности шагающих роботов}}

\section{Задачи работы}

В рамках работы рассматриваться проблема разработки конечностей для шагающих роботов с точки зрения подбора электроприводов и их управления. Сравниваться будут два типа электроприводов: заводские микро-сервоприводы с редуктором и бесколлекторные синхронные двигатели (BLDC). 

Требуется:
\begin{itemize}
    \item Рассчитать худший (по нагрузке) статический случай для конечностей 4-х ногого робота.
    \item Подобрать два электропривода удовлетворяющих по крутящему моменту. Для двух типов электроприводов разработать модель конечностей.
    \item Собрать физическую модель конечностей двух типов.
    \item Сравнить управляемость и механические характеристики конечностей двух типов.
\end{itemize}

\section{Актуальность работы}

Задача разработки конечностей для шагающих роботов настолько же важная, как и задача навигации роботов. Сегодня она актуальна, как никогда ранее. Всё в большей степени людей стараются заменять шагающими роботами для работ вроде общего тех. осмотра помещений, исследования местности вдали от дорог и цивилизации, помощи в устранении последствий катастроф. Открытость методик, исходных кодов и готовых рассчитанных моделей приведет к массовой разработке шагающих роботов не только крупными предприятиями, но и мелкими разработчиками.

\section{Анализ}

Для поставленных ранее задач можно сформировать последовательность действий, которые приведут к их решению.

\subsection{Рассчёт худшего статического случая}

"Худшим" случаем называется такой, при котором одному или нескольким приводам нужно приложить максимальный момент для поворота звена конечности в нужную сторону.

Для того чтобы определить худший случай, нужно вообще определиться с кинематикой конечности. Оптимальной кинематикой можно считать конечность с 3 степенями свободы:

\begin{figure}[ht]
    \centering
    
    \caption{Кинематика 4-х ногого робота, вид сбоку}
\end{figure}

Худшим случаем считается случай, в котором робот лежит на "животе" с выпрямленной конечностью. Чтобы подогнуть под себя конечность, нужно будет преодолеть момент $M_{worst}$ с учетом массы тела робота $m$.

\begin{figure}[ht]
    \centering
    
    \caption{Кинематика 4-х ногого робота, вид сбоку (худший случай)}
\end{figure}

При расчёте в первом приближении можно пренебречь трением и весами звеньев. Также можно учесть, что нагрузка, создаваемая массой тела робота будет распределена равномерно по всем 4-м ногам. Это значит что на одну ногу будет приходится лишь $\frac{1}{4}m$ тела робота.

Также, в первом приближении допустим, что тело робота может достигать 2-х килограмм. Большая часть веса придется на каркас конструкции, собранный из пластика. Меньшая часть веса придется на аккумулятор. Еще более маленькая часть придется на проводку и крепежи. Самыми легкими составляющими конструкции окажутся электронные компоненты.

При таком расчете можно считать что каждой ноге надо будет "поднять" около 0.25 кг веса. Тогда в худшем случае, приложенный момент вычисляется просто:
$$ M_{worst}=(l_{1}+l_{2}) m g $$
Здесь $l_1$ и $l_2$ - длины звеньев.

Мы можем подобрать длины звеньев таким образом, чтобы они обеспечивали достатучную для задач ходьбы рабочую область и одновременно наименьший требуемый момент:

\textit{*обосновать выбор именно таких длин звеньев, какие использую я}

\subsection{Подбор электроприводов}

Исходя из требуемых моментов были выбраны два вида электроприводов.

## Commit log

2019-11-24 Начал писать анализ работы
2019-12-08 Добавил в диплом инфу по стенду для измерения момента BLDC мотора
    [BGM5208-200-12.SLDPRT, Крепеж линейки.SLDPRT, Сборка стенда для BLDC.SLDASM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]
2020-02-19 day one of один_час_в_день_на_диплом_challenge
    [SERVO rds3115-3d v3.SLDPRT, TOWER PRO MG-995, ANALOG SERVO v2.SLDPRT, Втулка серво 1.SLDPRT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]
2020-02-21 Добавлена четырехзвенная передача
    [Колено-Узел3.SLDPRT, Колено-Узел4.SLDPRT, Колено-Узел5.SLDPRT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]
2020-02-22 Небольшие правки в ногу робота
    [Колено-Узел2.SLDPRT, Колено-Узел5.SLDPRT, Сборка Ноги.SLDASM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]
2020-02-23 Третье звено доделано версия 1
    [Звено 2 - Стержень несущий.SLDPRT, Колено-Узел.SLDPRT, Колено-Узел2.SLDPRT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]
2020-02-29 завершена первая версия ноги
    [Декор корпус.SLDPRT, Звено 2 - Стержень несущий.SLDPRT, Колено-Узел.SLDPRT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]
2020-03-05 Final leg
    [makeProjectedPlanarWire.x_t, Колено-Узел3.SLDPRT, Колено-Узел4.SLDPRT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]
2020-04-07 Ноги завершены, начат каркас тела робота
    [[Mirrored] Крепеж перхней фермы тела.SLDPRT, Крепеж перхней фермы тела.SLDPRT, Передний верхний профиль тела.SLDPRT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]
2020-05-18 добавил структуру диплома (заголовки)
2020-05-18 изменения в корпусе
2020-05-19 Написал одну секцию про механику ноги
2020-05-20 рефакторинг и еще немного текста
2020-05-20 Еще немного текста про механику и проектирование
2020-05-20 Немного про кинематику
2020-05-20 вставлены изображения в раздел кинематики
2020-05-22 немного добавки в третью главу
2020-05-23 Написал про четырехзвенник и прямую кинематику
2020-05-23 Начал писать про обратную кинематику
2020-05-24 Дописан пункт про обратную кинематику
2020-05-24 Дописана глава про кинематику
2020-05-24 Дополнена иллюстрациями глава 2
2020-05-26 Написал про протокол передачи данных
2020-05-27 Глава 6 дополнена программистскими штучками
2020-05-27 Цитирования и правки
2020-05-27 Правки правки
2020-05-27 Правки и убран мусор
2020-05-27 Еще немного правок
2020-05-27 Про протокол подробнее
2020-05-28 Изменено название работы
2020-05-29 Больше иллюстр. Подбор элпривода перенесен дальше
2020-05-29 Еще обльше верстки и иллюстраций
2020-05-31 Бета-версия завершенных чертежей робота
    [Adafruit PWM Servo Driver with PCA9685.SLDPRT, Arduino.SLDPRT, LM2596 DC-DC StepDown Converter v1.SLDPRT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]
2020-05-31 Дописана глава 2. Много иллюстрацие добавлено
2020-06-05 Большие правки перед зачетом по преддипломной прак
2020-06-08 Введение + иллюстрации и немного правок
2020-06-08 Начата одна глава и добавлена одна схема
2020-06-11 Заключение и глава про ходьбу дополнены
2020-06-11 Добавлен merger диплома с титульниками, создающий готовый для отправки файл
2020-06-12 Большой апдейт
2020-06-12 Исправлены некоторые опечатки и грамматика
2020-06-13 Исправлена грамматика и опечатки
2020-06-13 Нормальный текст про выбор кинематики + грамматика
2020-06-14 Отредачены актуальность и заключение
2020-06-14 Исправлены 1-ая глава, актуальность, заключение
2020-06-15 Вставлены фотографии сборки
2020-06-15 Компиляция
2020-06-15 Исправлены формулы
2020-06-16 Правки после консультации с науч. руководителем
2020-06-16 Новые правки после консультации
2020-06-16 После проверки правописания Spell Checker
2020-06-20 Полировка
